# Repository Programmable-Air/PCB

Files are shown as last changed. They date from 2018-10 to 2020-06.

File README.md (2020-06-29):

# PCB

## Pre-order at [CrowdSupply](https://www.crowdsupply.com/tinkrmind/programmable-air)

PCB for Programmable-Air

The electronics for Programmable-Air are pretty simple, as these things go. The PCB is composed of two boards that are connected by default but can be snapped off and used independently. The 'master' board contains an Arduino Nano, two pumps and IO. The 'slave' board contains three valves and the pressure sensor circuit. In this way, the 'master' board contains the brains and IO as well as the pressure sources while the 'slave' board contains the valves to control air flow and feedback from the pressure sensor. The 'master' board contains connectors to attach two more slave boards, thus allowing you to control three independent soft robots with the same Arduino. However, most of the time you'd probably only use the boards in their default configuration.

Below is the pin definition for the v0.5 of the board:

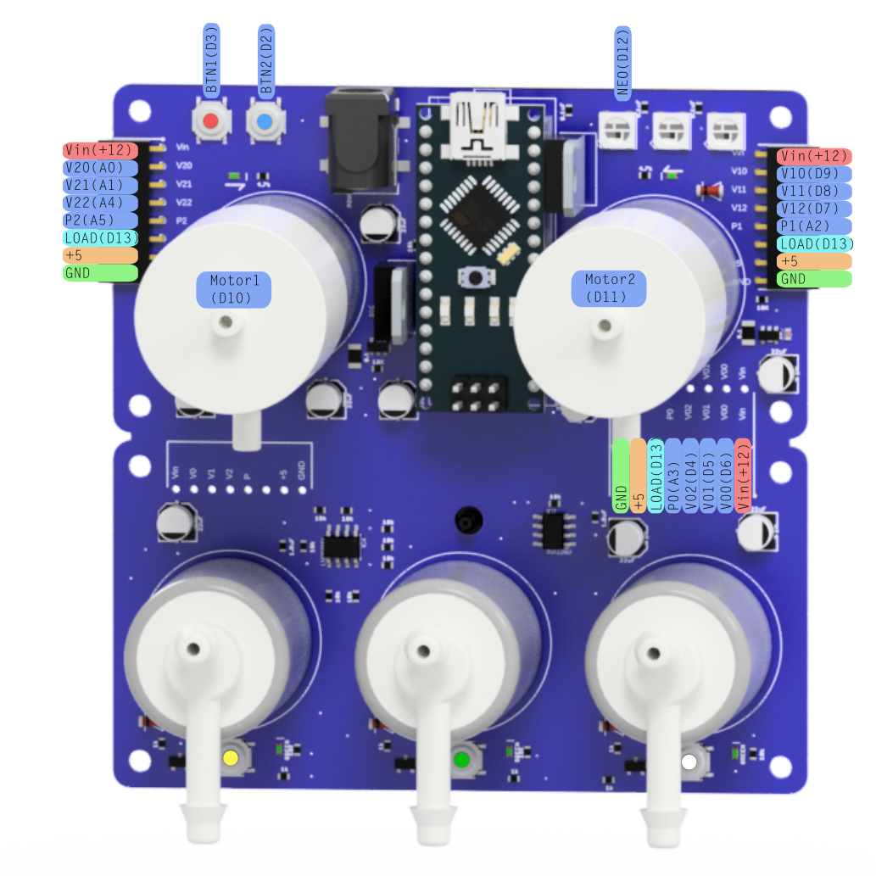
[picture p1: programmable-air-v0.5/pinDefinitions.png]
Programmable-Air PCB v0.5 Pin Definitions


Here are the functions of all the Pins:

* __Power:__
	* __Vin(+12V)__ - from the external power source
	* __+5V__ - Regulated 5V from Arduino's linear 5V regulator
	* __GND__ - Common ground for all signals

* __Connections on master board:__
	* __D10__ - Drives the base of the transistor for Motor 1
	* __D11__ - Drives the base of the transistor for Motor 2
	* __D12__ - Drives the three onboard neopixels(for debugging and such)
	* __D13__ - Drives the base of the Load transistor. The collector of the Load is broken out as Load. You can connect it to an external pump or relay for regulating them.
	* __D2__ - Connected to the __blue__ button, pulled up using the internal 20K resistor and connects to ground when button is pressed
	* __D3__ - Connected to the __red__ button, pulled up using the internal 20K resistor and connects to ground when button is pressed
	* __AREF__ - Connected to a LM4040 +5V voltage reference

* __Connections to slave boards__
	* __Board 0__
		* __A3__ - Pressure sensor output(on the valve board). Can be used as a GPIO if slave board is not connected. Range~ 1V-4V
		* __D4__ - Drives Valve #02 via a transistor(on the valve board). Can be used as a GPIO if slave board is not connected.
		* __D5__ - Drives Valve #01 via a transistor(on the valve board). Can be used as a GPIO if slave board is not connected.
		* __D6__ - Drives Valve #00 via a transistor(on the valve board). Can be used as a GPIO if slave board is not connected.

	* __Board 1__
		 * __A2__ - Pressure sensor output(on the valve board). Can be used as a GPIO if slave board is not connected. Range~ 1V-4V
		 * __D9__ - Drives Valve #12 via a transistor(on the valve board). Can be used as a GPIO if slave board is not connected.
		 * __D8__ - Drives Valve #11 via a transistor(on the valve board). Can be used as a GPIO if slave board is not connected.
		 * __D7__ - Drives Valve #10 via a transistor(on the valve board). Can be used as a GPIO if slave board is not connected.

	* __Board 2__
		 * __A5__ - Pressure sensor output(on the valve board). Can be used as a GPIO if slave board is not connected. Range~ 1V-4V
		 * __A4__ - Drives Valve #22 via a transistor(on the valve board). Can be used as a GPIO if slave board is not connected.
		 * __A1__ - Drives Valve #21 via a transistor(on the valve board). Can be used as a GPIO if slave board is not connected.
		 * __A0__ - Drives Valve #20 via a transistor(on the valve board). Can be used as a GPIO if slave board is not connected.

The yellow, green and white button are connected to the base of the transistors driving their respective valves and override the signal from the Arduino. They are intended to be used for testing a new soft robot without any coding.

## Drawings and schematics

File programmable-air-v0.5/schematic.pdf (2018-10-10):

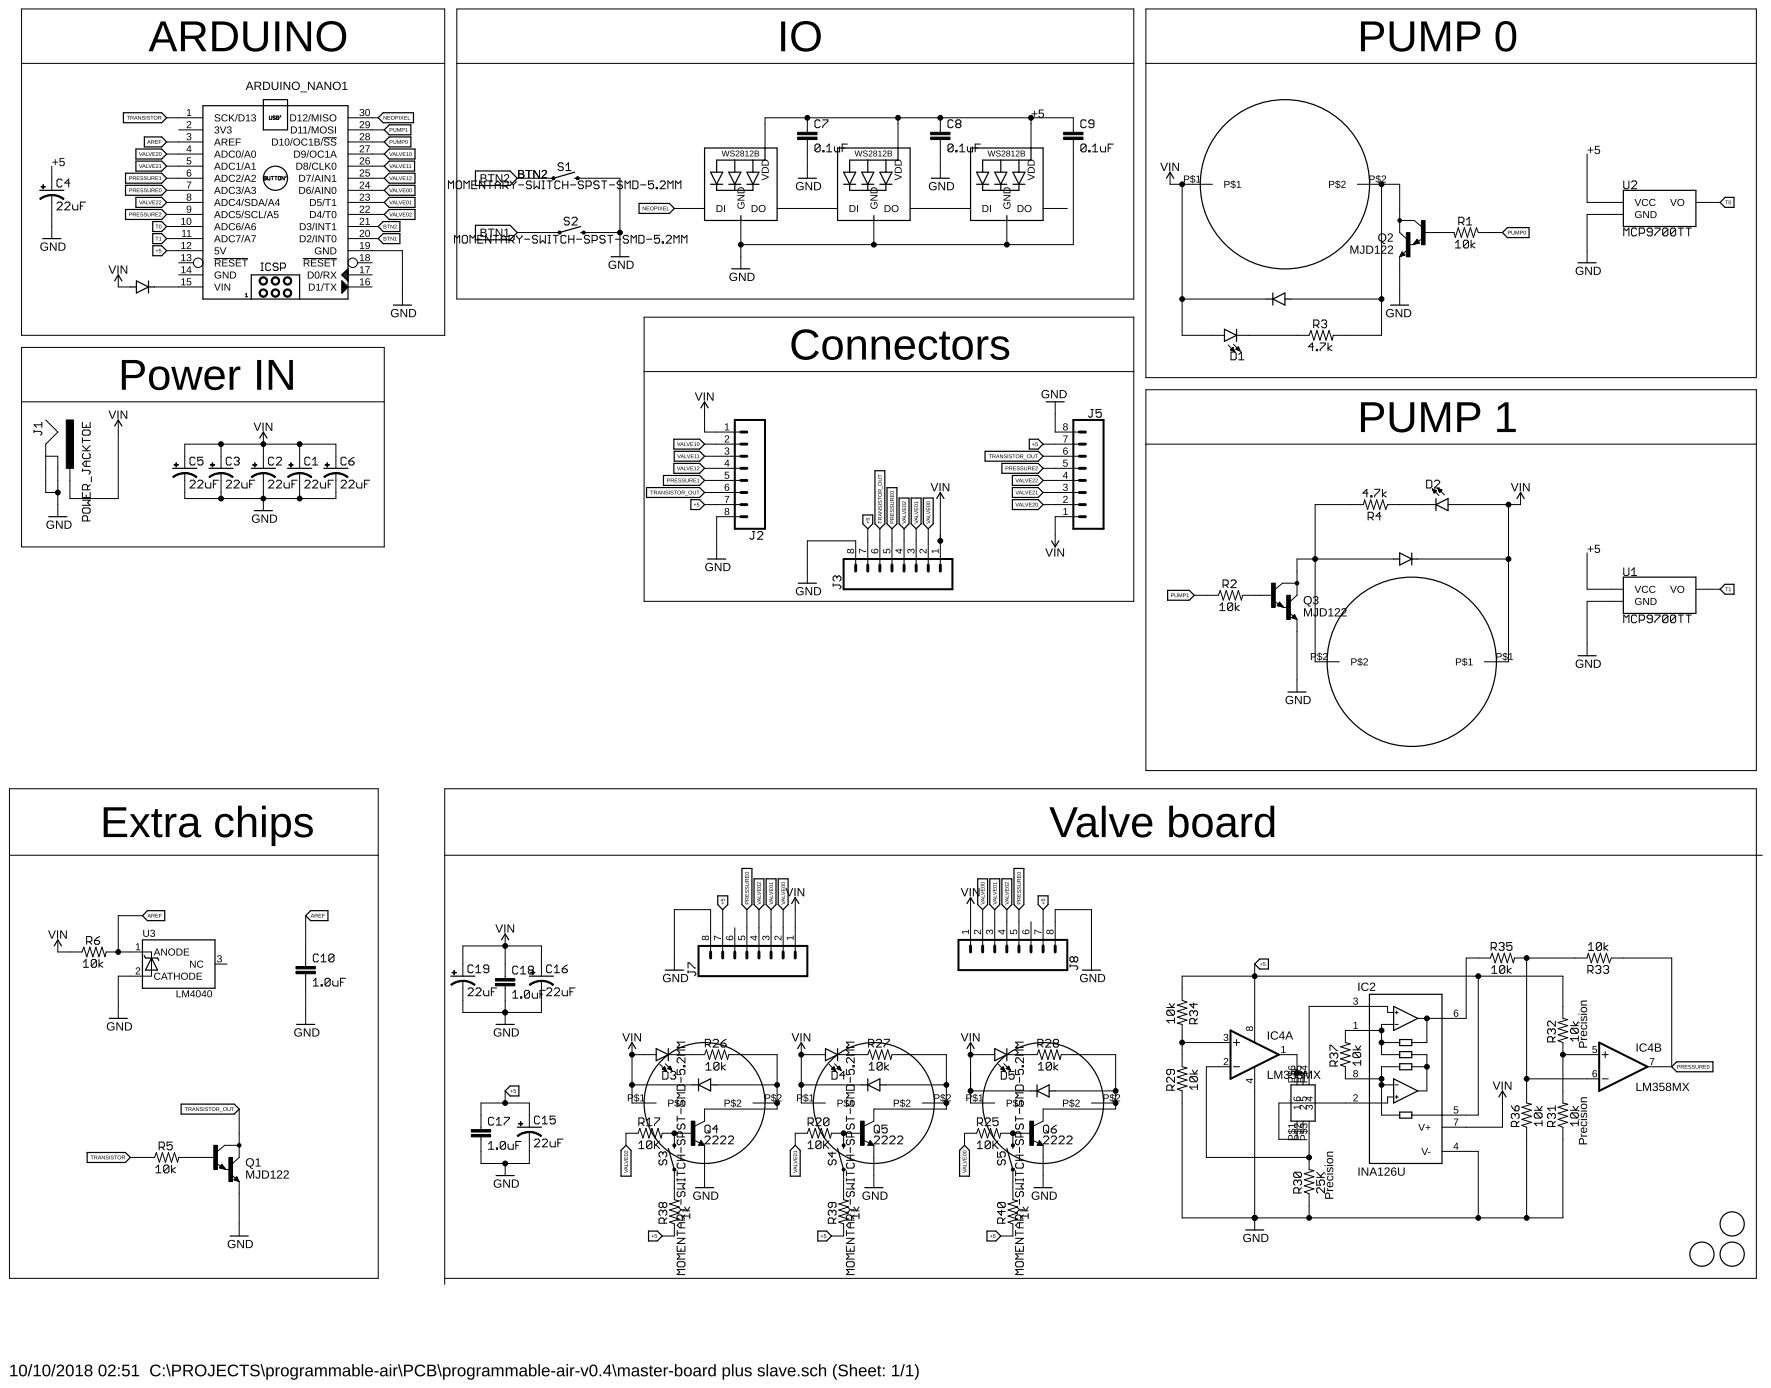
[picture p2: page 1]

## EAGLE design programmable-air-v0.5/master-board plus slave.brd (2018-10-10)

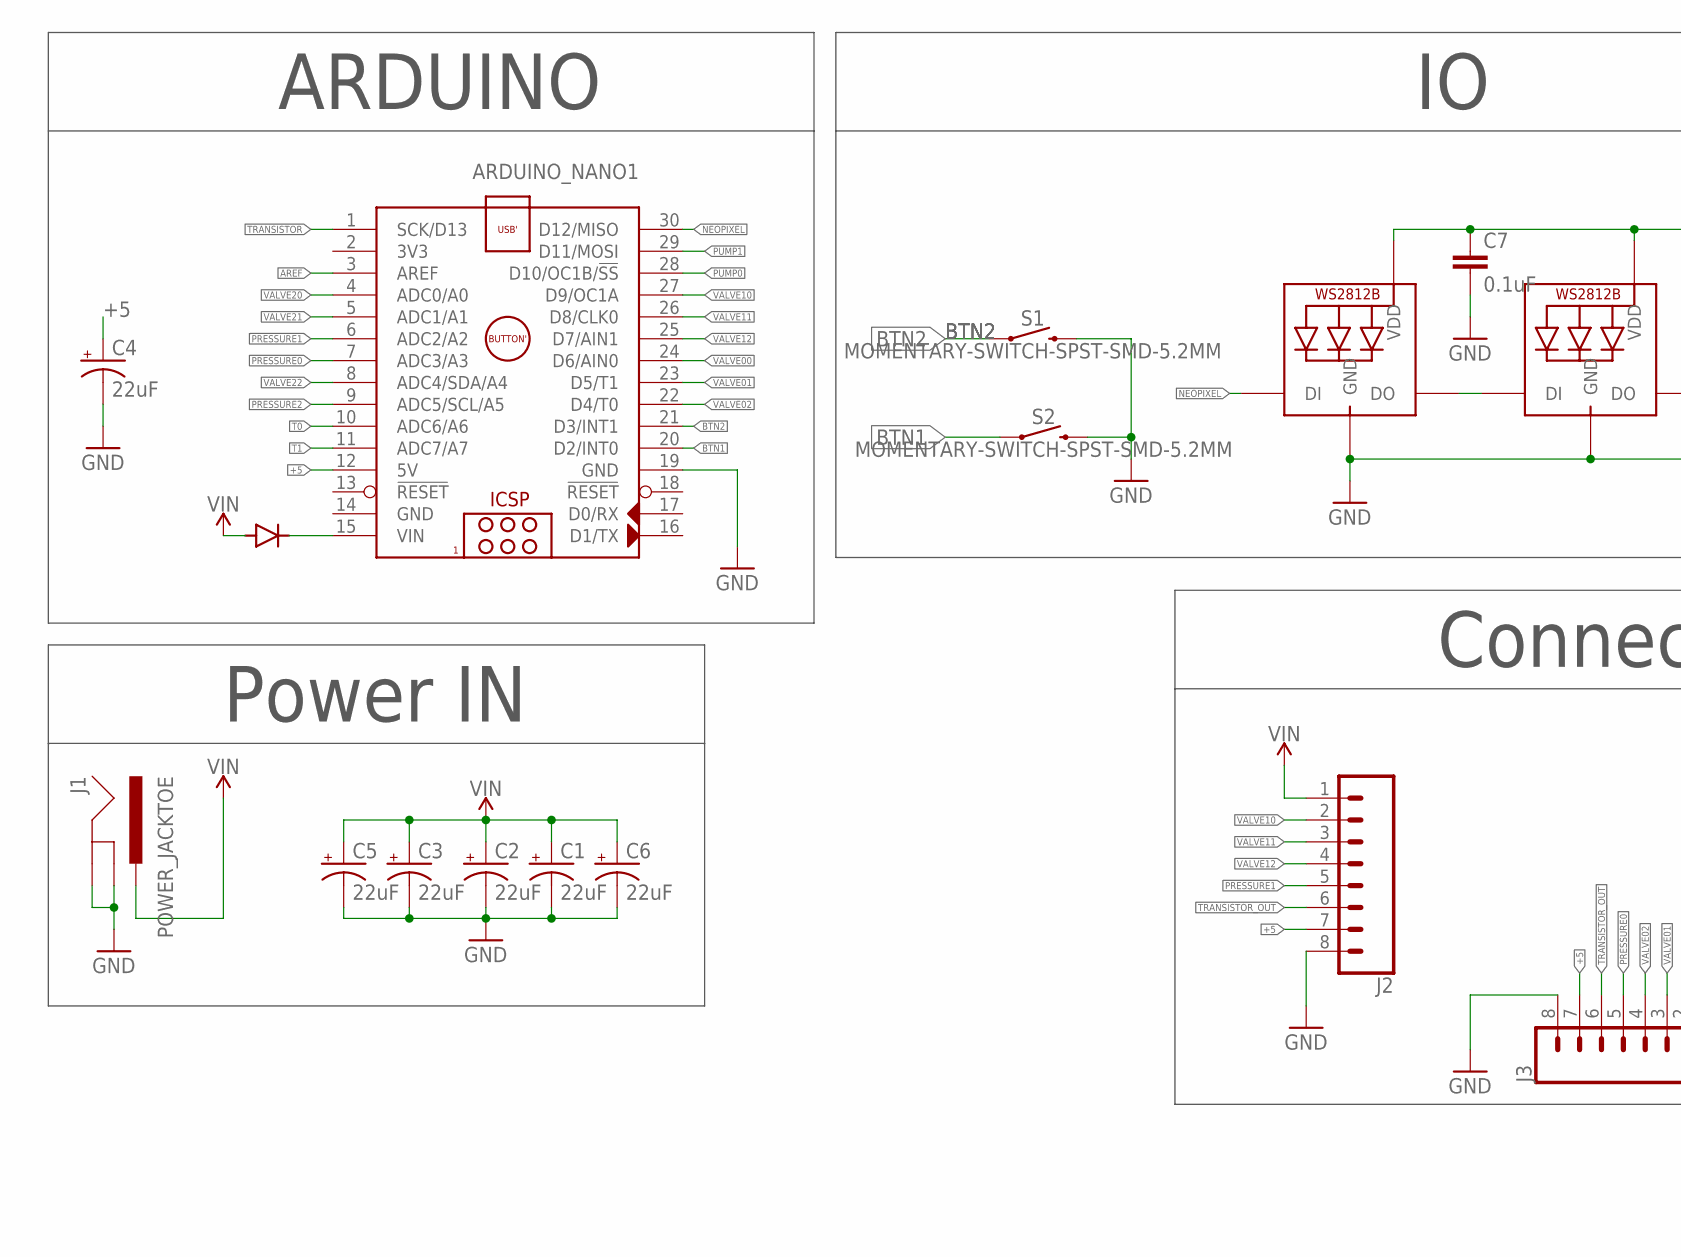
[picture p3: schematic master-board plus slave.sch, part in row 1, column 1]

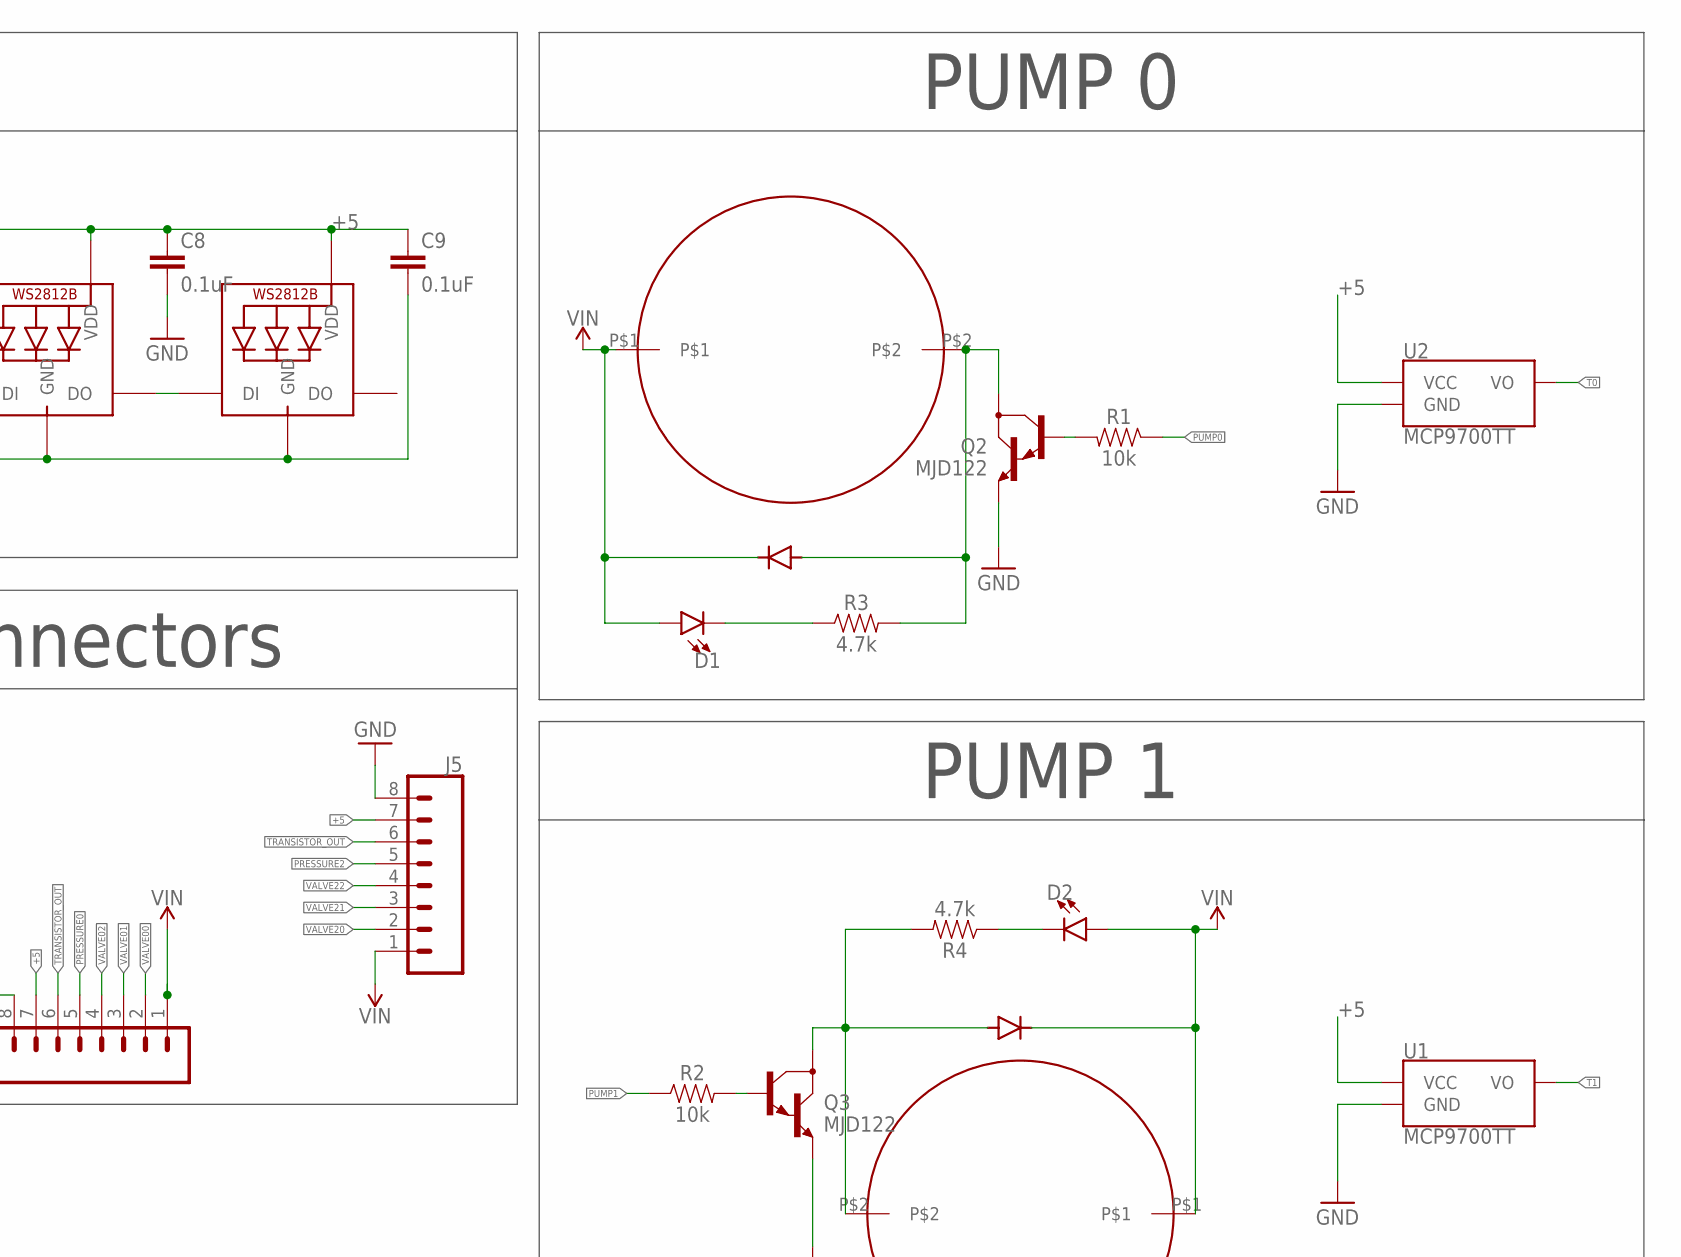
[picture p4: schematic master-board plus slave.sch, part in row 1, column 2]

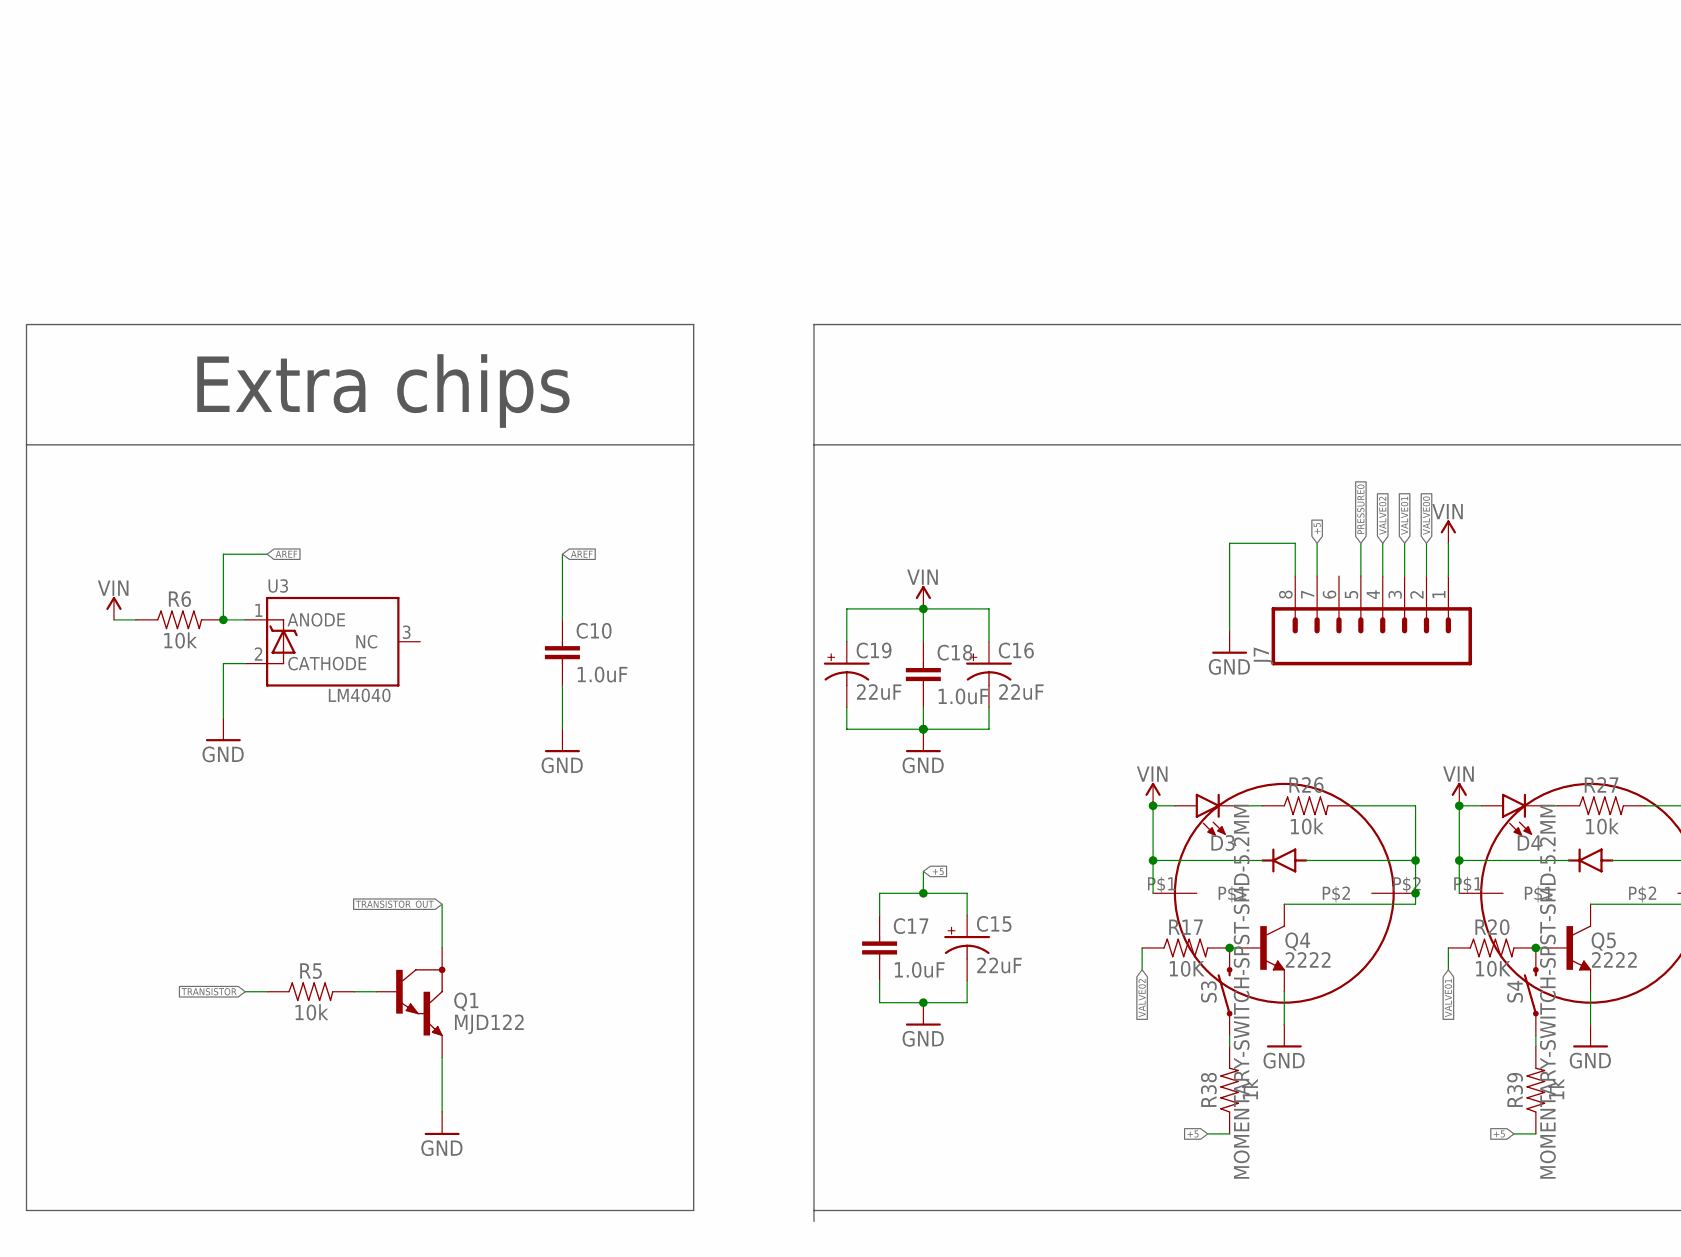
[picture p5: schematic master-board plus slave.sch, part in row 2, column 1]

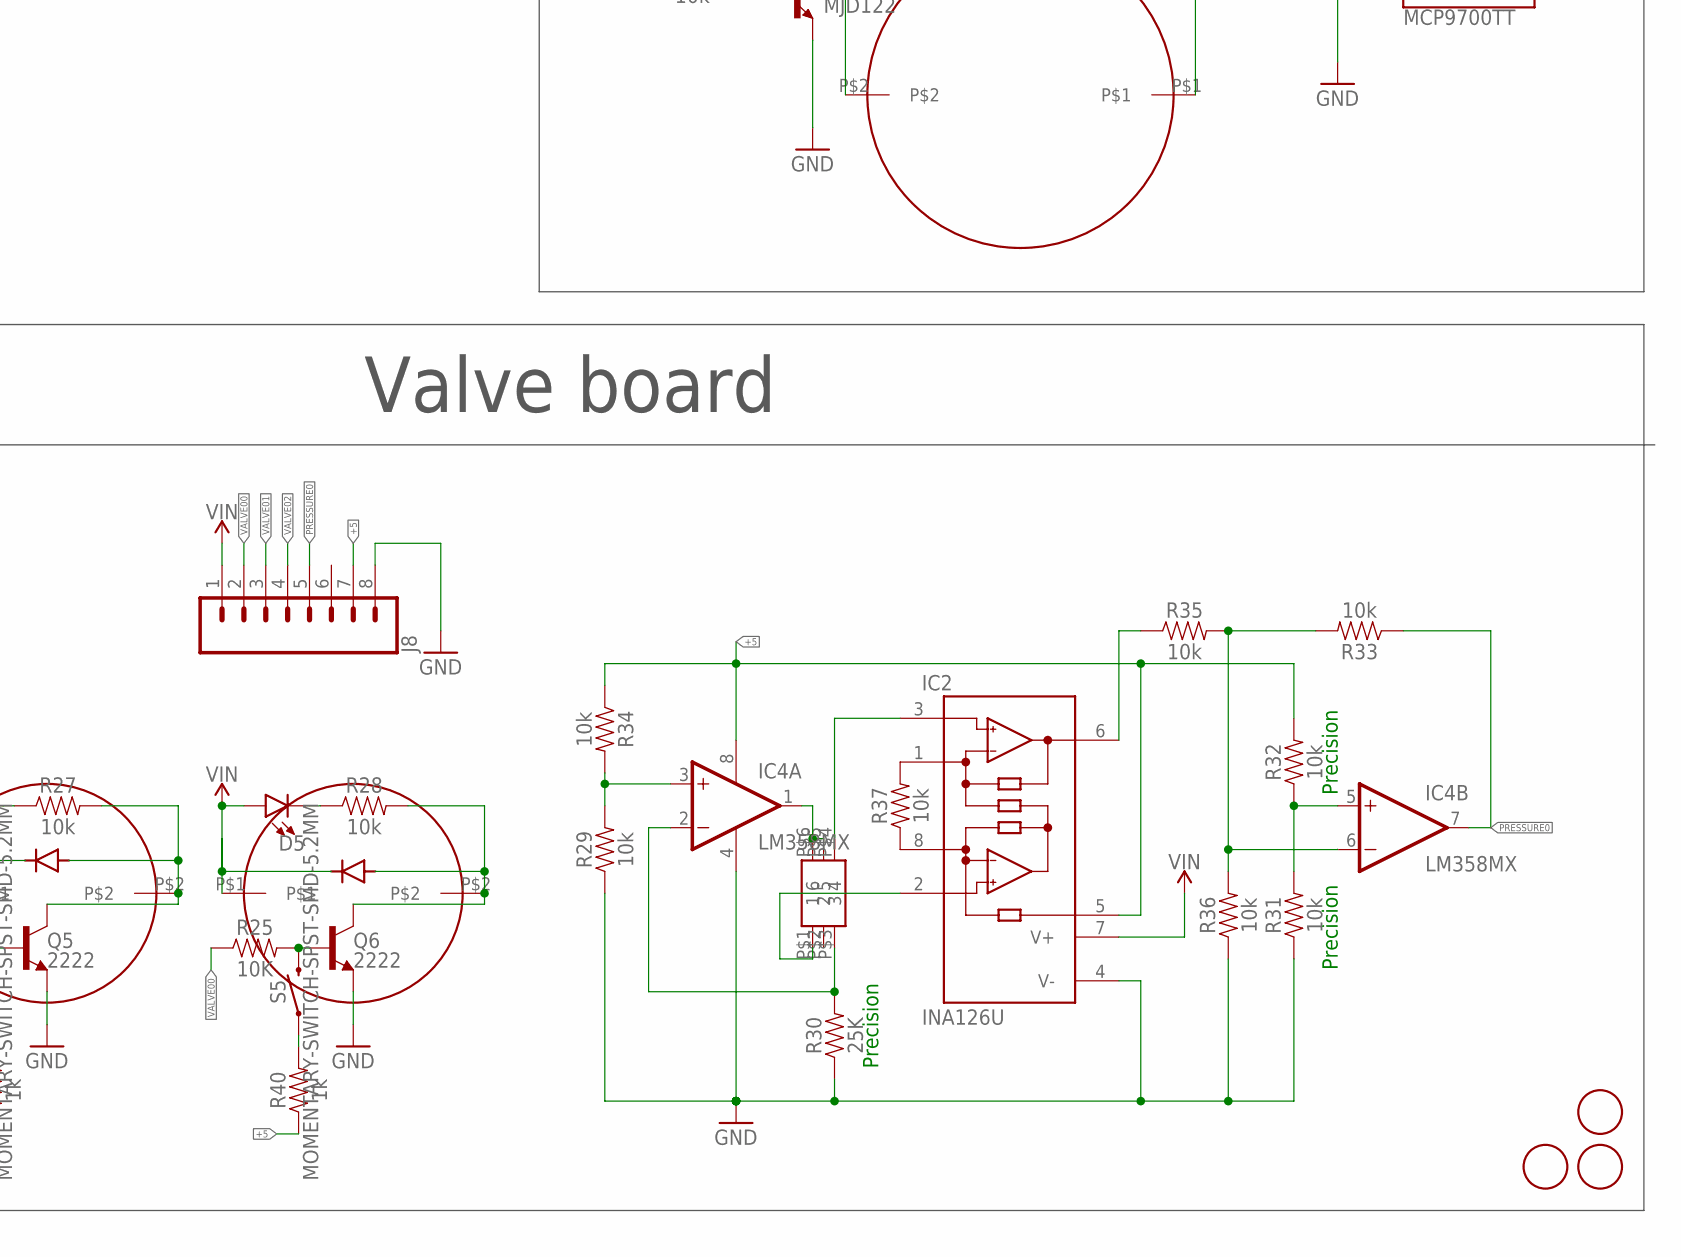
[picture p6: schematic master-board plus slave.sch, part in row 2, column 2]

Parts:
ARDUINO_NANO1: ARDUINO_NANO
C1, C2, C3, C4, C5, C6, C15, C16, C19: 22uF; PANASONIC_C
C7, C8, C9: 0.1uF; 0603
C10, C17, C18: 1.0uF; 0603
D1, D2, D3, D4, D5: LED0603; LED-0603
IC2: INA126U; SO08
IC4: LM358MX; SO08
J1: POWER_JACKTOE; POWER_JACK_SMD_OVERPASTE_TOE
J2: CONN_08FLIPPED; 1X08
J3: CONN_08"; 1X08
J5: CONN_081X08_FEMALE_FLIPPED; 1X08_FEMALE_FLIPPED
J7: CONN_08; 1X08_MALE_FLIPPED
J8: CONN_08NO_SILK_FEMALE_PTH; 1X08_NO_SILK
LED1, LED2, LED3: WS2812B5050; WS2812B
Q1, Q2, Q3: MJD122; DPAK
Q4, Q5, Q6: 2222; SOT23-3
R1, R2, R5, R6, R26, R27, R28, R29, R31, R32, R33, R34, R35, R36, R37: 10k; 0603
R3, R4: 4.7k; 0603
R17, R20, R25: 10K; 0603
R30: 25K; 0603
R38, R39, R40: 1k; 0603
S1, S2, S3, S4, S5: MOMENTARY-SWITCH-SPST-SMD-5.2MM; TACTILE_SWITCH_SMD_5.2MM
U1, U2: MCP9700TT; SOT23-3
U3: LM4040; SOT23-3
U$1, U$2: AIYIMA-PUMP-A5F083; A5F083
U$3, U$4, U$7, U$20, U$21, U$22: IN4148; SOD123
U$10, U$11, U$12: FIDUCIAL; FIDUCIAL_1MM
U$17, U$18, U$19: CJV23-SOLENOID-VALVE; CJV23
U$23: 2SMPP-03

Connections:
+5: ARDUINO_NANO1.12 (5V), C4.+, C7.1, C8.1, C9.1, C15.+, C17.1, IC2.5 (REF), IC4.8 (V+), J2.7, J3.7, J5.7, J7.7, J8.7, LED1.1-VDD (VDD), LED2.1-VDD (VDD), LED3.1-VDD (VDD), R32.2, R34.1, R38.1, R39.1, R40.1, U1.1 (VCC), U2.1 (VCC)
AREF: ARDUINO_NANO1.3 (AREF), C10.1, R6.2, U3.1 (ANODE)
BTN1: ARDUINO_NANO1.20 (D2/INT0), S2.1
BTN2: ARDUINO_NANO1.21 (D3/INT1), S1.1
GND: ARDUINO_NANO1.14 (GND), ARDUINO_NANO1.19 (GND), C1.-, C2.-, C3.-, C4.-, C5.-, C6.-, C7.2, C8.2, C9.2, C10.2, C15.-, C16.-, C17.2, C18.2, C19.-, IC2.4 (V-), IC4.4 (V-), J1.GND (GNDBREAK), J1.P$4 (GND), J2.8, J3.8, J5.8, J7.8, J8.8, LED1.3-GND (GND), LED2.3-GND (GND), LED3.3-GND (GND), Q1.3 (E), Q2.3 (E), Q3.3 (E), Q4.2 (E), Q5.2 (E), Q6.2 (E), R29.1, R30.1, R31.1, R36.1, S1.3 (2), S2.3 (2), U1.3 (GND), U2.3 (GND), U3.2 (CATHODE)
unnamed: ARDUINO_NANO1.15 (VIN), U$7.C
unnamed: Q3.1 (B), R2.2
unnamed: Q2.1 (B), R1.2
unnamed: Q2.4 (C), R3.2, U$1.P$2, U$3.A
unnamed: Q3.4 (C), R4.2, U$2.P$2, U$4.A
unnamed: Q1.1 (B), R5.2
unnamed: D1.C, R3.1
unnamed: D2.C, R4.1
unnamed: LED2.2-DOUT (DO), LED3.4-DIN (DI)
unnamed: LED1.2-DOUT (DO), LED2.4-DIN (DI)
unnamed: Q4.1 (B), R17.2, S3.3 (2)
unnamed: Q5.1 (B), R20.2, S4.3 (2)
unnamed: Q6.1 (B), R25.2, S5.3 (2)
unnamed: Q6.3 (C), R28.2, U$19.P$2, U$22.A
unnamed: Q5.3 (C), R27.2, U$18.P$2, U$21.A
unnamed: Q4.3 (C), R26.2, U$17.P$2, U$20.A
unnamed: D5.C, R28.1
unnamed: D4.C, R27.1
unnamed: D3.C, R26.1
unnamed: IC2.2 (-IN), U$23.P$1 (1)
unnamed: IC4.1 (OUT), U$23.P$5 (5), U$23.P$6 (6)
unnamed: IC2.3 (+IN), U$23.P$4 (4)
unnamed: IC4.3 (+IN), R29.2, R34.2
unnamed: IC2.8 (RG), R37.1
unnamed: IC2.1 (RG), R37.2
unnamed: IC4.6 (-IN), R33.2, R35.2, R36.2
unnamed: IC4.5 (+IN), R31.2, R32.1
unnamed: IC4.2 (-IN), R30.2, U$23.P$3 (3)
unnamed: IC2.6 (OUT), R35.1
unnamed: R38.2, S3.1
unnamed: R39.2, S4.1
unnamed: R40.2, S5.1
NEOPIXEL: ARDUINO_NANO1.30 (D12/MISO), LED1.4-DIN (DI)
PRESSURE0: ARDUINO_NANO1.7 (ADC3/A3), IC4.7 (OUT), J3.5, J7.5, J8.5, R33.1
PRESSURE1: ARDUINO_NANO1.6 (ADC2/A2), J2.5
PRESSURE2: ARDUINO_NANO1.9 (ADC5/SCL/A5), J5.5
PUMP0: ARDUINO_NANO1.28 (D10/OC1B/!SS), R1.1
PUMP1: ARDUINO_NANO1.29 (D11/MOSI), R2.1
T0: ARDUINO_NANO1.10 (ADC6/A6), U2.2 (VO)
T1: ARDUINO_NANO1.11 (ADC7/A7), U1.2 (VO)
TRANSISTOR: ARDUINO_NANO1.1 (SCK/D13), R5.1
TRANSISTOR_OUT: J2.6, J3.6, J5.6, Q1.4 (C)
VALVE00: ARDUINO_NANO1.24 (D6/AIN0), J3.2, J7.2, J8.2, R25.1
VALVE01: ARDUINO_NANO1.23 (D5/T1), J3.3, J7.3, J8.3, R20.1
VALVE02: ARDUINO_NANO1.22 (D4/T0), J3.4, J7.4, J8.4, R17.1
VALVE10: ARDUINO_NANO1.27 (D9/OC1A), J2.2
VALVE11: ARDUINO_NANO1.26 (D8/CLK0), J2.3
VALVE12: ARDUINO_NANO1.25 (D7/AIN1), J2.4
VALVE20: ARDUINO_NANO1.4 (ADC0/A0), J5.2
VALVE21: ARDUINO_NANO1.5 (ADC1/A1), J5.3
VALVE22: ARDUINO_NANO1.8 (ADC4/SDA/A4), J5.4
VIN: C1.+, C2.+, C3.+, C5.+, C6.+, C16.+, C18.1, C19.+, D1.A, D2.A, D3.A, D4.A, D5.A, IC2.7 (V+), J1.VIN0 (PWR), J2.1, J3.1, J5.1, J7.1, J8.1, R6.1, U$1.P$1, U$2.P$1, U$3.C, U$4.C, U$7.A, U$17.P$1, U$18.P$1, U$19.P$1, U$20.C, U$21.C, U$22.C

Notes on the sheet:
Precision
Power IN
PUMP 0
PUMP 1
ARDUINO
Connectors
Valve board
Extra chips

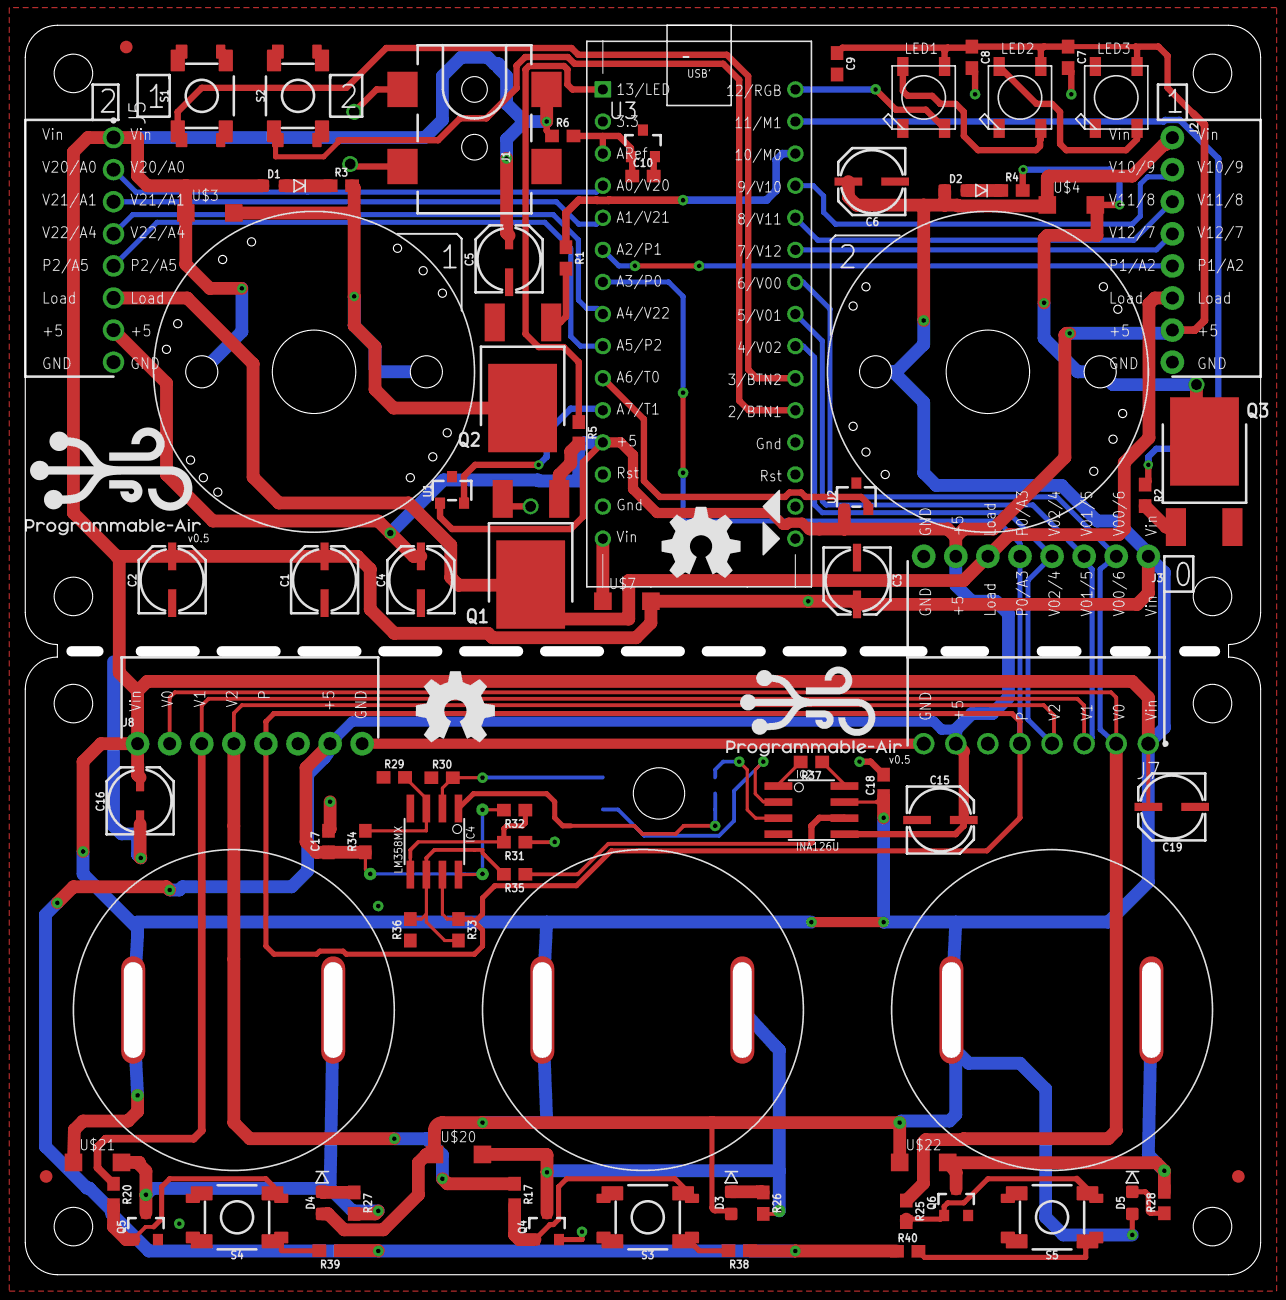
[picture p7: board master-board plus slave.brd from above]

Board: 2 copper layers, 97.8 x 98.9 mm, 85 parts (0 on the bottom side), 57 nets.

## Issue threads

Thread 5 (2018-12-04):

Update pin definition image

tinkrmind, 2018-12-04:
Current image is of PCBv0.3 instead of v0.5 and in perspective view instead of orthographic view.

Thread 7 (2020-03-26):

Ardunio Nano 33 IOT

Gidget19893161, 2020-03-26:
PCB board does not seem to work with ardunio nano 33 iot. Seems to be an issue with the manual valve buttons. They dont work with th nano 33 iot board plugged in but when the regular nano is plugged in, it works just fine.

mmehta15, 2021-11-29:
Hey There,
Can you share your code for using IOT. I am new with arduinos and It would be a great help to learn. (shifting maintain pressure code from regular nano to nano IOT)

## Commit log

2018-10-10 Initial Commit after sending v0.5 for production
    [master-board plus slave.brd, master-board plus slave.sch]
2018-12-04 Added pin definitions and updated readme to contain pin definitions

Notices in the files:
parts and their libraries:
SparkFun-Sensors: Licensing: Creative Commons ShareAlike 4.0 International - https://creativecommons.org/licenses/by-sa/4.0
